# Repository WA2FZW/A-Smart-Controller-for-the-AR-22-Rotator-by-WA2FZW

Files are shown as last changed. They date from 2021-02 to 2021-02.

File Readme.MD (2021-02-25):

A Smart Controller for the AR-22 Rotator by WA2FZW
Version 5.4

The AR-22 rotator controller is an Arduino Uno based controller for the old
CDE AR-22 antenna rotator which replaces the clunk-clunk controller that the
original used.

The main features include the ability to turn the antenna in 1, 5 or 10
degree increments and the ability to control it with many of the rotator
control programs available such as the N1MM Rotor program.

The files provided here include the latest version of the software, a manual
describing how to build and use the controller and the Gerber files needed
to fabricate the 2 custom PCBs used.

Version 5.3

No changes to the software (Version 5.2 is the latest software version), but
Neal (WA9WYI) discovered a mistake on the power supply PCB; the pins on the
LM7812 regulator were reversed. The Gerber files for the power supply PCB
are corrected and identified as Version 5.3.

Document Update 9/4/2020:

Added information about the commands available on the serial interface. Not
sure why I never listed them in the original!

Update Jan 04, 2021 - Fixed a couple of typos in the docmentation and added
a "Table of Contents".

Version 5.4 - 2/24/2021

I made a number of changes to both the hardware and software and finally
fixed a problem that has been bugging me since the intial version!

Hardware Changes

In the hardware, I added more filtering on the power supply board and on
the controller board I added snubbing diodes across the relay coils (I
thought they were built into the relays; NOT) and added a bypass capacitor
in an effort to reduce the noise on the rotator pulse line.

One additional change on the controller PCB was to add a header connected
to the TX2/RX2 serial interface on the Arduino Mega. This is not used yet,
but I plan to add elevation control using a separate processor.

Software Changes

In the software, I made some changes to the timeout logic to deal with two
problems.

One problem this solves is the fact that there is some inertial delay when
the rotator initially turns on; the bigger the antenna, the more inertia!
The second problem was that sometimes the rotator was stopping with the cam
switch in the closed position which caused an immediate pulse upon the next
startup and the inertia delay was causing an immediate timeout.

Now when the rotator starts (or reverses direction), the cam pulse timeout
value is set to 2 seconds by the symbol INITIAL_TIMEOUT in the header file.
Once the controller has seen 2 cam pulses, the timeout value reverts to the
value of ROTATOR_TIMEOUT.

I also made a few changes in the code to improve performance and I added the
hooks for an interface to an elevation controller for my satellite antenna.

Note that the Version 5.4 software will run on the older hardware (Version
5.2 and later).

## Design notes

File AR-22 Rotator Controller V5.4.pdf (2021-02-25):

- Page 1 -

## A Smart Controller for the AR-22 Rotator Version 05.4

## © John Price – WA2FZW

## Table of Contents

- Page 2 -

- Page 3 -

- Page 4 -

## License Information

This documentation and the associated software are published under General Public License version 3. Please feel free to distribute it, hack it, or do anything else you like to it. I would ask, however that is you make any cool improvements you let me know via any of the websites on which I have published this or by email at WA2FZW@ARRL.net.

## Introduction

I had just finished up two Arduino (https://www.arduino.cc/) based ham radio projects; a BitX-40 (http://www.hfsigs.com/) QRP transceiver and a magnetic loop antenna and controller when I received an email from Mike, WV2ZOW asking if it might be possible to design a computer based controller for the old CDE AR-22 (http://www.radiomanual.info/schemi/ACC_rotator/CDE_AR-22R_user.pdf) (clunk-clunk) rotator. Without even a second thought, I replied something to the effect of “Piece of cake”! After all, I had spent a number of years at the phone factory (AT&T) computerizing things that were never designed to be computerized, so this seemed to be a project right up my alley.

The overall objective was to be able to control the rotator either manually or with the N1MM+ contest logging and rotator control software. (https://n1mm.hamdocs.com/tiki-index.php)

I looked at a number of similar projects online and one in the ARRL’s Arduino for Ham Radio (https://www.arrl.org/shop/Arduino-for-Ham-Radio) book and although I got a few good ideas, didn’t find any that really looked like they would accomplish what I wanted to do. My main issue with most of them was the software. I looked at one controller that has some 14K lines of code. My software has about 1,600 lines and about half of those are comments and blank lines inserted for clarity.

Well, it turned out not to be quite as simple as I first thought (definitely an understatement), but overall, it wasn’t totally impossible.

Thanks to Mike (WV2ZOW unfortunately now a SK) for all his help with the electrical issues encountered along the way.

Here, I’ll describe the hardware and software used in the project. The reader can build this exactly as described or use this description as a model for a different approach. I’ll try to point out all the wrong assumptions and mistakes I made along the way.

- Page 5 -

## Revision History

Changes in Version 2.0

In version 1.0, the azimuth was completely controlled by pulses generated by the cam operated switch inside the rotator itself. Those pulses were sent approximately every 6° of rotation.

In Version 2.0, interrupts from a software timer were used to generate pseudo index pulses approximately every 1° of rotation, which allowed the azimuth to be set within 1° (plus or minus a slight error).

Changes in Version 2.1

Version 2.1 included three hardware changes and one software change.

The first change which included both hardware and software was done to fix the problem of the Arduino rebooting whenever the N1MM+ Rotor program or the Arduino IDE serial monitor was started. A toggle switch labeled “Run/Update” was added to the back panel. This switch, when closed, places a 10uF capacitor between the Arduino’s reset pin and ground. It gobbles up the very brief reset pulse sent by the serial connection whenever the N1MM+ Rotor program or the serial monitor is started.

The reset pulse is generated via a connection on the Arduino board between the DTR (Data Terminal Ready) line from the serial interface to the reset line.

That same short reset pulse is also sent from the Arduino IDE whenever we need to load new software into the Arduino, thus the switch must be opened to disconnect the capacitor whenever new software needs to be loaded.

Associated with this modification, the back panel “Reset” button was disconnected from the Arduino’s reset pin and moved to D19 (an interrupt enabled pin). Pressing the button will now do two things; first, it will save the currentAzimuth then perform a software initiated reboot.

The second minor hardware change was to add diode D2 (I renumbered them on the schematic also) between the output of the LM7812 regulator and the Arduino’s Vin pin. The connection for the Power indicator LED is now between the regulator and D2.

- Page 6 -

This was done because in Version 1.0, the LED would light when the controller was connected to a computer via the USB connection regardless of whether the internal power supply was turned on or not. This was because when the Arduino was connected to the computer via the USB port, there was approximately 4.5V on the Vin pin; that was totally unexpected. Now, the Power LED only lights when the internal power supply is on. When the USB connection is present, the LCD display will continue to light up regardless of the state of the internal supply.

Note that the Version 2.1 or Version 3.0 software will run on controllers that do not have these hardware modifications.

A third hardware modification was to build the power supply on a separate circuit board that mounts on top of the interconnect board. The circuitry was not changed (other than the addition of ‘D2’); this modification just made a little more total real estate available and made it simpler to wire it all up.

Changes in Version 2.2

In version 2.2, two new functions were added, and the timing parameters were tweaked.

The first new function is Backup(), which moves the rotator slightly off the end stop whenever it times out (either in normal use or calibration). The second is Ck_Reboot(), which checks to see if the operator pushed the reset button on the back panel. It contains the same logic that was originally coded in the Loop() function, but since it also needed to be checked in the Calibrate() function, it was converted into a stand-alone function.

In conjunction with the addition of the Backup() function a new definition was added called CAL_ADJUSTMENT, which defines the number of degrees to back off the end stop.

The timing tweaks included reducing the timer interrupts from 141mS to 140mS and changing the rotator timeout from 1 second to 850mS.

- Page 7 -

Changes in Version 3.0

After adding the timer interrupt in Version 2.0, I noticed that the rotator was not turning a full 360° when commanded to do so (either via the serial interface or the encoder). Hooking the rotator up to the original clunk-clunk box, I also discovered that the same thing was happening; even though the original controller recorded 60 clunks, the rotator did not turn a full 360°.

Making some careful measurements, I found that it was coming up about 9° short. Doing a little math, I calculated that the cam switch was actually producing pulses about every 5.85° instead of the advertised 6°.

This necessitated a complete overhaul of the azimuth computations.

Rather than incrementing or decrementing the currentAzimuth by a whole degree for every timer or cam pulse received, the azimuth is adjusted by 0.975 degrees (5.85/6) for each pulse. Rather than attempting to use floating point math, all the internal azimuths and adjustment factors are multiplied by 1000 internally and the long data type is used to store the numbers.

Also in Version 3.0, because of all the things that might need to be tweaked for a particular rotator, I moved the definition of the number of degrees per cam pulse and all the variables associated with the timer interrupt interval, cam pulse detection, LCD parameters and encoder pin definitions to the My_Rotator.h header file to make it easier for someone to find and tweak these parameters.

Changes in Version 4.0

Although I finished the initial version of this project some 6 months ago, I hadn’t actually used the controller in a real operating environment until I finally got a 6 meter beam on the roof just before the 2018 ARRL June VHF contest. In operating the contest, the first thing I discovered was that it took an awful lot of turns of the azimuth (encoder) knob to turn the antenna 180°. The second thing I noticed was that in the brief times when I was repositioning my fingers on the knob to turn it more, sometimes the azimuth would be saved before I had finished setting the final target azimuth.

- Page 8 -

So, in Version 4.0, I made 2 hardware/software changes. First, I added a 3 position SPDT (center off) toggle switch to the front panel. This switch along with some software changes allows the operator to select the number of degrees to increment (or decrement) the target azimuth when turning the encoder knob. The increment can now be set to 1°, 5°, or 10°. A symbol definition (AZ_SW_INSTALLED) was added to the My_Rotator.h file to indicate whether or not said switch is actually installed.

If the switch is not installed, the azimuth increment is determined by the value set in the My_Rotator.h file for DEFAULT_INCR; it is set to 5° in the distributed software but can be changed to any value you like.

A second hardware change I made was to add another LED to the front panel which will indicate that the currentAzimuth has been saved in the EEPROM.

A second software change was to modify the algorithm for saving the azimuth. As noted above, I noticed that it would sometimes get saved before I had finished setting a new target azimuth. Now the azimuth will be saved 10 seconds from the last time the rotator stopped turning. This can be adjusted by changing the value of the symbol EEPROM_TIMEOUT in the “My_Rotator.h” file.

Changes in Version 4.1

In Version 4.1, I made a slight change to the calibration logic. In previous versions, when a timeout occurred due to missing a cam pulse, the currentAzimuth would get set to either 0° or 360° based on which direction the rotator was turning. It the timeout did not occur due to it hitting the end stop, it would now be way out of calibration.

Doing a calibration after such a timeout would often cause the rotator to turn through almost a full rotation to re-calibrate itself.

In order to correct this, a new variable, lastGoodAzimuth is introduced. This gets set to the currentAzimuth only after successfully seeing a sync pulse (hard or soft). In the calibration function, this variable is used to determine which way to turn the rotator to do the calibration instead of the possibly erroneous currentAzimuth.

- Page 9 -

Changes in Version 5.0 & 5.1

There are no significant software changes in Version 5.0 other than to reassign some of the Arduino pin numbers used.

What did change is the hardware. Using my newly acquired knowledge of how to design printed circuit boards, I decided to replace the hand-wired boards used in the first two of these I built. That also allowed me to fix a hardware bug in the first one that was just too hard to fix because of the way I built the hand-wired board for that one.

Version 5.1 fixed some bugs on the PCB and in the software.

Changes in Version 5.2

When testing Version 5.1 with a 2nd rotator, a problem showed up in that the rotator was hitting the mechanical end stop with the cam switch in the closed position, which caused a never-ending pulse to be sent to the controller and thus, the expected timeout at the end stop would never occur.

I made a number of attempts to fix this in the software without any luck and finally decided to re-design the entire pulse detection circuit. This also required a couple more minor tweaks in the code.

Cleaning up the pulse detection hardware and software also allowed me to further tweak the timing parameters.

Changes in Version 5.3

Neal (WA9WYI) discovered an interesting problem on the Version 5.0 power supply PCB; the pins for the LM7812 regulator were reversed! This was due to a rather DUMB mistake by yours truly. The redesigned power supply PCB is Version 5.3 and the Gerber files on GitHub have been updated to correct the problem.

If you have one of the older PCBs, you can mount the regulator vertically, upside down on the top side of the board or mount it on the bottom. The heat sink is not really necessary.

The schematic did not change.

- Page 10 -

Changes in Version 5.4

Version 5.4 makes some changes to both the software and the hardware. The primary goal of this version was to fix a problem that has been there since the initial version; periodically, when using the controller with a PC program such as the N1MM Rotor program (https://n1mmwp.hamdocs.com/setup/interfacing/) or the SatPC32 satellite tracking program (http://www.dk1tb.de/manual_e.htm) the USB connection between the controller and the PC would drop. It seems to be fixed!

Hardware Changes

In the hardware, I added more filtering on the power supply board and on the controller board I added snubbing diodes across the relay coils (I thought they were built into the relays; NOT) and added a bypass capacitor in an effort to reduce the noise on the rotator pulse line.

One additional change on the controller PCB was to add a header connected to the TX2/RX2 serial interface on the Arduino Mega. This is not used yet, but I plan to add elevation control using a separate processor.

Software Changes

In the software, I made some changes to the timeout logic to deal with two problems.

One problem this solves is the fact that there is some inertial delay when the rotator initially turns on; the bigger the antenna, the more inertia!

The second problem was that sometimes the rotator was stopping with the cam switch in the closed position which caused an immediate pulse upon the next startup and the inertia delay was causing an immediate timeout.

Now when the rotator starts (or reverses direction), the cam pulse timeout value is set to 2 seconds by the symbol INITIAL_TIMEOUT in the header file. Once the controller has seen 2 cam pulses, the timeout value reverts to the value of ROTATOR_TIMEOUT.

I also made a few changes in the code to improve performance and I added the hooks for an interface to an elevation controller for my satellite antenna.

- Page 11 -

Note that the Version 5.4 software will run on the older hardware.

## Controlling the Rotator from a PC

The N1MM+ Rotator Control Program

The original intent of the smart controller was to allow it to work with the N1MM Rotor program. (https://n1mmwp.hamdocs.com/) That program supports a number of different types of rotators and communications protocols. Two of those protocols seem to be fairly standard. Those are Yaesu’s GS-232 protocol (http://www.radiomanual.info/schemi/YAESU_ACC/Yaesu_GS-23_GS-232_user.pdf) and HyGain’s DCU-1 protocol. (https://www.hamsupply.com/wp-content/uploads/2015/11/Rotor-EZ-Protocol.pdf)

I originally thought it might be a good idea to design the AR-22 controller so that I could support either protocol, which might allow it to be used with other contest logging programs, but in the end, decided that the GS-232 protocol was much easier to implement and it seemed to have more capabilities than the DCU-1 protocol, including support for 2-axis systems (not implemented in the AR-22 software).

The N1MM Rotor program doesn’t even use the full basic GS-232 protocol. The only commands implemented seem to be:

Mnnn | Turn the rotator to the azimuth specified by nnn.
C | Ask the rotator what its current azimuth is.
S | Stop the current command.

The N1MM Rotor Control program can be used as a stand-alone controller, or it can be used in conjunction with the N1MM+ Contest Logging program, which determines an approximate antenna azimuth based on the coordinates of the station using the software and the station being communicated with’s call sign.

Since the AR-22 software emulates the Yaesu protocol, when setting the N1MM Rotor program up, you have to tell it that the AR-22 is a Yaesu type rotator. You can also give it a unique name.

The N1MM Rotor program communicates with the AR-22 controller using a USB-2.0 port running at 9600 baud (which can’t be changed in the N1MM Rotor program). The N1MM+ Logging software also supports the ability to network a number of computers together for multi-operator contest operations.

- Page 12 -

Satellite Tracking with SatPC32

More recently, I’ve started to play with the amateur satellites and have been using the SatPC32 (http://www.dk1tb.de/indexeng.htm) program to track them and control my Icom IC-9700. SatPC32 is the current gold standard satellite tracking program. It has a rotator interface named ServerSDX which works with the controller. The setup is a bit confusing, but how to set the rotator up is very clearly explained in the help files for the program.

ServerSDX also supports elevation control and in Version 5.4 of the software and hardware I’ve added some hooks to add elevation control capability to the unit. For a bit more information about this see the Coming Attractions section of this document.

Controlling the Rotator via the Serial Interface

Although the rotator controller can be used with the N1MM Rotor program as described above, it can actually be controlled by any terminal emulator program (or the Arduino IDE’s Serial Monitor) capable of communicating with the processor via the USB port.

The USB port is set to operate at 9600 baud in the software as that is the baud rate hard coded in the N1MM Rotor program (you can change it if you like).

There are actually a number of other commands that can be sent to the controller in addition to those listed above; here is the complete list:

'A' or ‘S’ Stop command; cancels the last command and rotation
'C' | Ask for current azimuth; responds with “AZ=nnn”.
'L' | Rotate CCW to endstop
'R' | Rotate CW to endstop
'Maaa' | Rotate to specific azimuth
'F' | Start full calibration
'Zaaa' | Initialize azimuths
‘Waaa ee’ Turn to a specific azimuth and elevation

The ‘Z’ (zap) command is not part of the Yaesu protocol. I added it to facilitate testing and debugging. It sets both the currentAzimuth and targetAzimuth variables to the specified value (limited to the valid range of 0 to 360 of course) and saves the setting in the EEPROM.

- Page 13 -

Other Rotator Control Possibilities

Since the AR-22 controller software implements all of the basic Yaesu rotator commands, it will probably work with any PC based rotator control software which supports the GS-232 protocol.

Please note that the complete GS-232 command set is not implemented as some of the commands are just cannot be applied to the AR-22 rotator.

For anyone proficient at writing code for the PC or maybe a Raspberry Pi, you could also write your own program. If anyone does so, please let me know!

## The Controller Hardware

There are only a few major components in the controller hardware; specifically:

- The Arduino Mega2560 R3 (https://store.arduino.cc/usa/arduino-mega-2560-rev3) processor.
- An I2C 1602 2 line by 16 character LCD display. (https://www.amazon.com/SunFounder-Serial-Module-Display-Arduino/dp/B019K5X53O?hvadid=312760964359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)
- A Keyes KY-040 Rotary Encoder (http://henrysbench.capnfatz.com/henrys-bench/arduino-sensors-and-input/keyes-ky-040-arduino-rotary-encoder-user-manual/)
- A power supply to provide AC for the rotator motor and DC to power the Arduino and its peripherals.
- A custom shield containing the motor control relays and a circuit to convert the MOTOR_INDEX pulse from AC to DC plus the interconnections between the peripherals and the Arduino’s I/O pins.
- A custom shield containing the power supply circuitry.

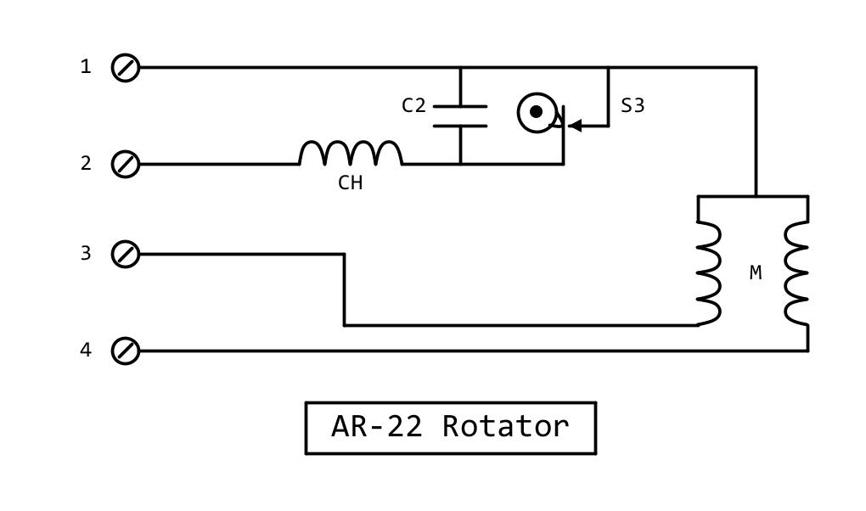
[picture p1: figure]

- Page 14 -

The Rotator Itself

Here is the schematic for the electrical components of the AR-22 rotator itself:

‘C2’ is 0.22uF @ 400V, and ‘CH’ is 15 turns of wire 3/8” in diameter.

In the original controller box, terminal ‘1’ is connected to one side of a (not center) tapped transformer, and terminal ‘2’ is connected to the other side of the transformer through the clunk-clunk solenoid.

Grounding terminal ‘3’ or ‘4’ starts the motor rotating in one direction or the other.

‘S3’ is operated by a cam and sends a pulse to the control box approximately every 6° of rotation.

The transformer used in the original controller is a custom transformer that CDE must have designed specifically for the controller (their main business was always capacitors and transformers). The original transformer provided about 36V on one side of the tap (connected to terminal ‘1’ on the rotator) when the motor wasn’t running, and 6.3V on the other side of the tap (for the #47 light bulb). The motor voltage is about 28V when the motor is operating.

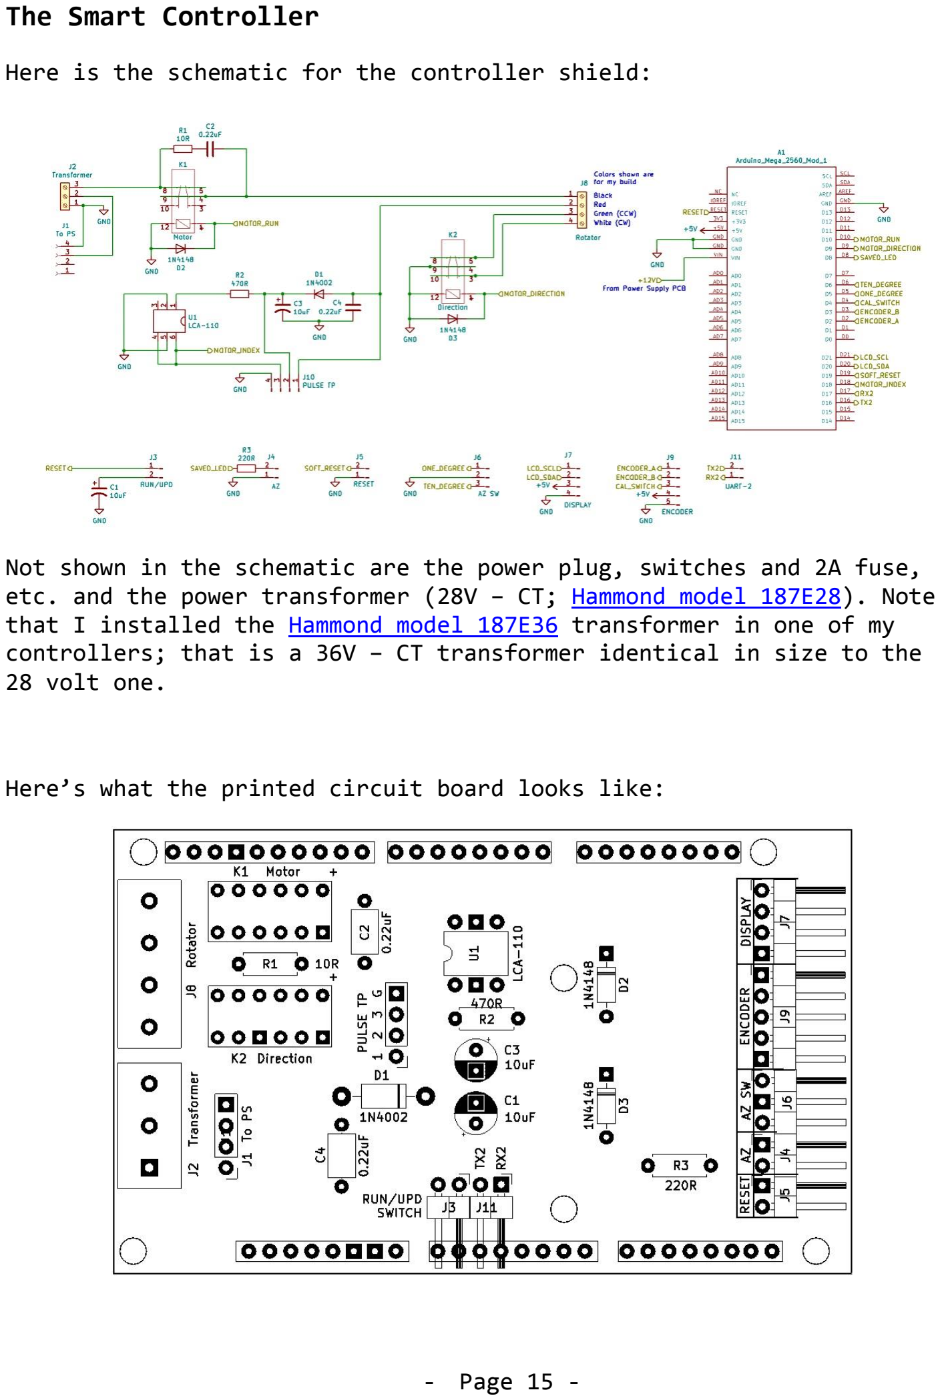
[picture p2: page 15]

- Page 15 -

The Smart Controller

Here is the schematic for the controller shield:

Not shown in the schematic are the power plug, switches and 2A fuse, etc. and the power transformer (28V – CT; Hammond model 187E28). (https://www.mouser.com/ProductDetail/Hammond-Manufacturing/187E28?qs=PRAnc%252blXlHhlx%2FRo63C%252bsw%3D%3D) Note that I installed the Hammond model 187E36 (https://www.mouser.com/ProductDetail/Hammond-Manufacturing/187E36/) transformer in one of my controllers; that is a 36V – CT transformer identical in size to the 28 volt one.

Here’s what the printed circuit board looks like:

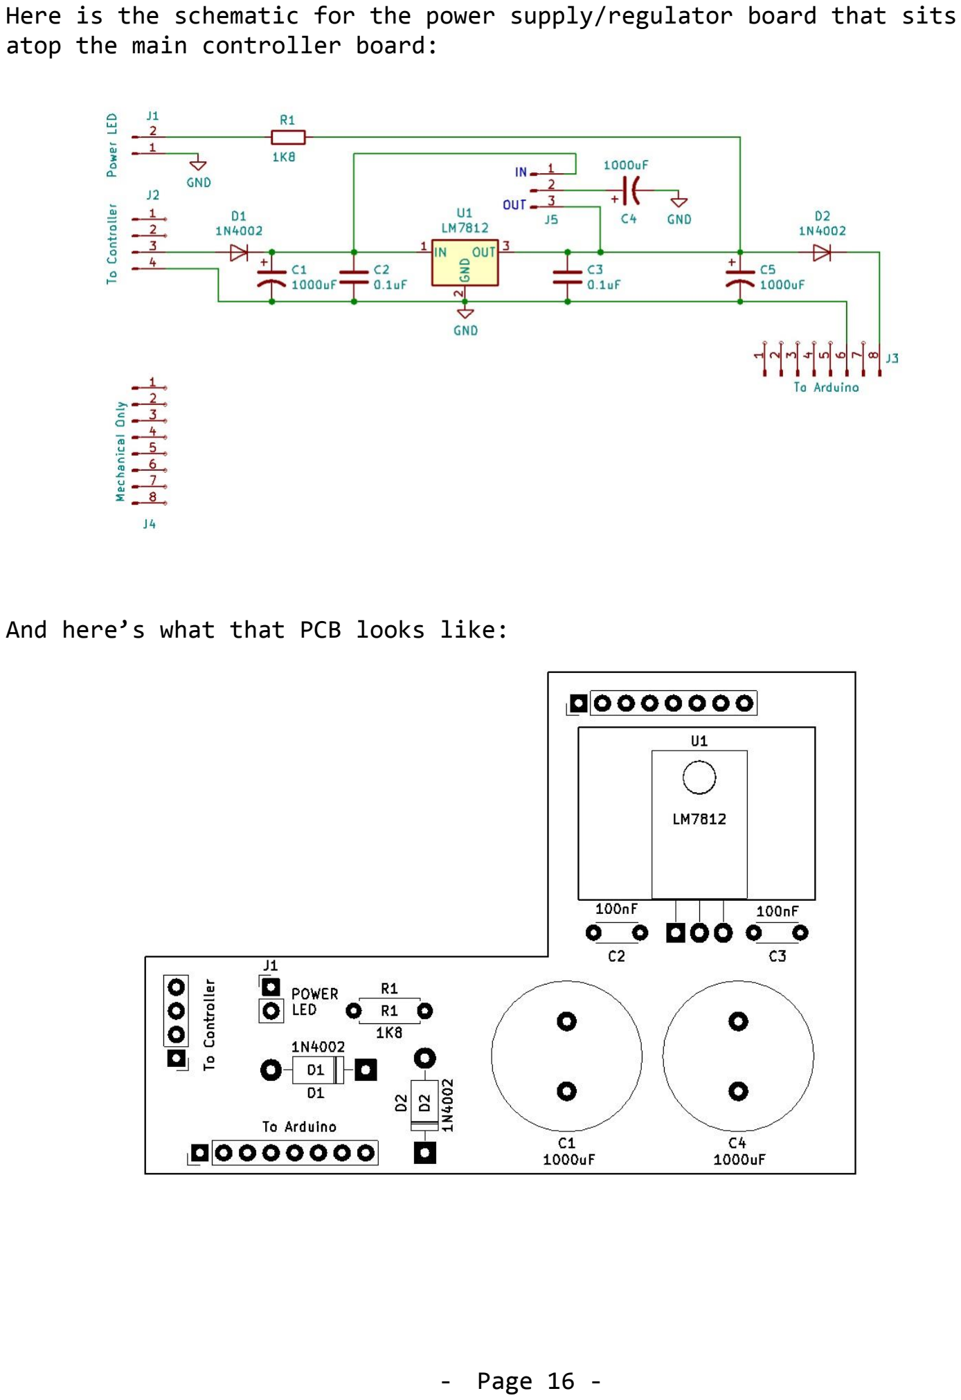
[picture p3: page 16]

- Page 16 -

Here is the schematic for the power supply/regulator board that sits atop the main controller board:

And here’s what that PCB looks like:

- Page 17 -

In the original clunk-clunk box, power was only applied to the power transformer when the dial was turned to start the rotator moving. Here, I not only use the transformer to power the rotator motor, but also as part of the DC power supply for the Arduino and its associated components, so it will always be turned on.

The original controller included a thermal protection switch on the primary of the power transformer; the smart controller omits it. In years of using the AR-22, I never had it activate. I believe it primarily came into play in the case where the rotator hit the mechanical end stop and the operator did not manually move the solenoid lever on the bottom of the box to calibrate the controller within a reasonable amount of time.

I determined that the thermal switch was unnecessary in the smart controller as the transformer used seems more robust than the original transformer and the software shuts down the motor automatically whenever the end stop is hit.

The top half of the transformer secondary provides 28 volts to the motor through ‘K1’, and grounding the other end of one or the other of the motor coils via ‘K2’ determines the direction of rotation. In the original clunk-clunk box, that was done by one of the cleverest mechanical switches I’ve ever seen that was part of the dial mechanism.

Here, the software will set the direction of rotation by activating (or not activating) ‘K2’. After a slight delay, ‘K1’ will be then be activated to start the rotation.

The relays I used (https://www.jameco.com/webapp/wcs/stores/servlet/ProductDisplay?catalogId=10001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) for ‘K1’ and ‘K2’ have 5V coils and contacts rated for 2A. The rotator motor draws just a bit over 2A, so since the relays are actually DPDT relays, I’m using both sets of contacts just to be on the conservative side. The relay coils draw 30mA, so they can be operated directly from the Arduino I/O pins, which are rated for a maximum of 40mA.

Note the combination of a 10Ω resistor and 0.22uF capacitor across the ‘K1’ contacts. This RC circuit prevents arcing of the ‘K1’ relay contacts when the motor is turned off. There is no such protection on the direction relay (‘K2’) as that one is never operated by the software while power is being supplied to the rotator through ‘K1’.

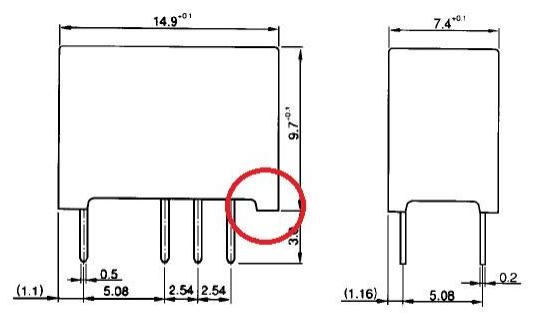
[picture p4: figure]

- Page 18 -

Something to note about these relays; they have little bumps on the bottom side corners as shown here:

If you’re going to solder them into the board, it’s not a problem, but they don’t socket well. I used a pair of flat cutters to cut the bumps off, but be careful on the end where the pins are close to the corner.

Terminal ‘2’ on the rotator is used to send pulses back to the controller via a cam operated switch that is closed momentarily every time the rotator moves about 6°. In Version 5.2, the entire pulse detection circuit was modified to use a solid state relay in place of the reed relay formerly used.

‘C3’ is the motor starting capacitor (https://www.amazon.com/gp/product/B00EQI3HZ2/ref=od_aui_detailpages00?ie=UTF8&psc=1) (not shown on the schematic; it is connected between terminals 3 and 4 of the rotator connection) and has a value of approximately 140uF and an operating voltage of 165VAC.

Summary of Arduino input/output pin usage

These are the pin assignments for the Arduino Mega 2560:

- D0 | USB Interface Receive
- D1 | USB Interface Transmit
- D2 | ENCODER_PIN_B
- D3 | ENCODER_PIN_A
- D4 | CAL_SWITCH (encoder pushbutton)
- D5 | ONE_DEGREE (1 degree switch)
- D6 | TEN_DEGREE (10 degree switch)

- Page 19 -
- D8 | SAVED_LED (Azimuth saved LED)
- D9 | MOTOR_DIRECTION (Relay ‘K2’)
- D10 | MOTOR_RUN (Relay ‘K1’)
- D11 | Reserved for Timer1 PWM output signals
- D12 | Reserved for Timer1 PWM output signals
- D13 | Reserved for Timer1 PWM output signals
- D16 | UART #2 Transmit (for the elevation controller interface)
- D17 | UART #2 Receive (for the elevation controller interface)
- D18 | MOTOR_INDEX (Interrupt enabled pin )
- D19 | SOFT_RESET_PIN (Interrupt enabled pin)
- D20 | LCD_SDA (I2C Data Line)
- D21 | LCD_SCL (I2C Clock Line)

Note that some encoders found online are wired backwards. If you have that issue, simply flip-flop the pin definitions for pins ‘A’ and ‘B’.

## Construction

The Controller Board

The relays and headers to connect the Arduino to the LCD, rotary encoder and a few other things are all mounted on the main controller board.

Besides changing the reed relay to an SSR in Version 5.2, I also added the “PULSE TP” header to the board to make it convenient to use an oscilloscope to look at the raw pulse from the rotator, the rectified and filtered pulse and the signal going to pin D18 of the Arduino.

The pins are numbered 1 to 3 on the PCB:

1. The pulse line directly from the rotator
2. The rectified and filtered (10uF) pulse from the rotator
3. The output of the LCA-110 SSR

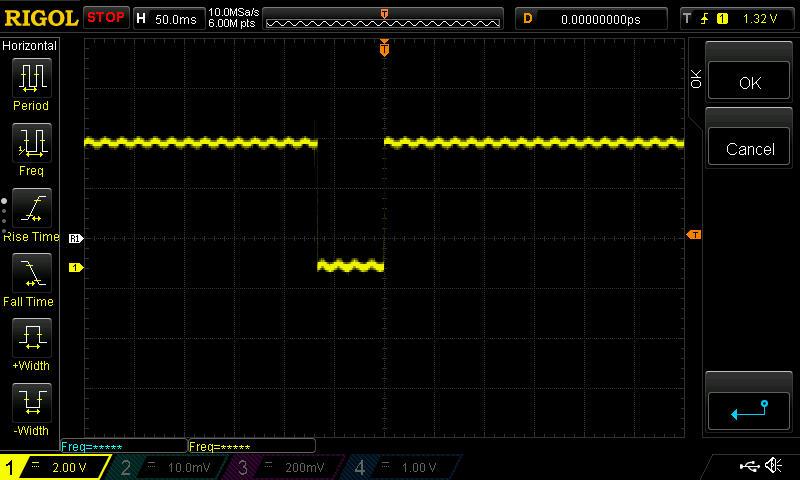
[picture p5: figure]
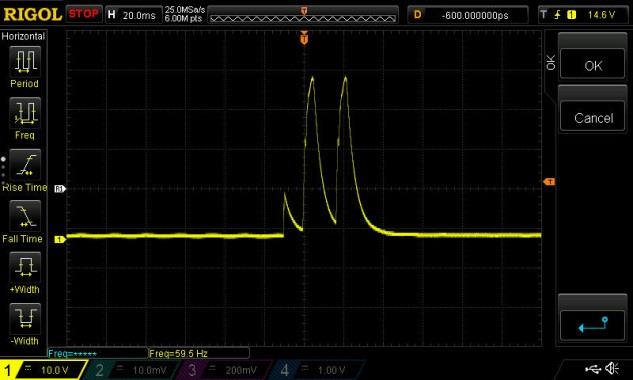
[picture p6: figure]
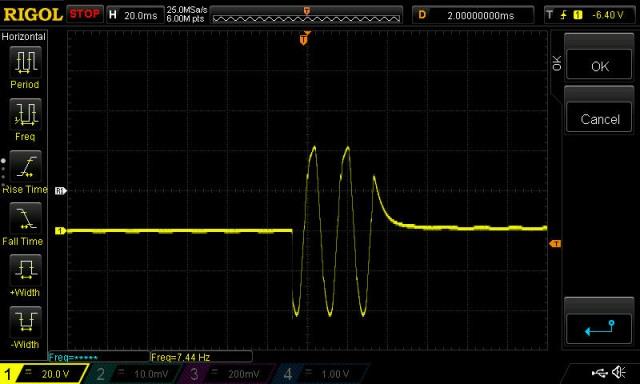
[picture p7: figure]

- Page 20 -

Here are some scope traces taken at the test points; this is the output of the LCA-110 SSR, which is what the processor sees (Test Point #3):

And here are the scope traces for the raw pulse from the rotator (Test Point #1) and the rectified and filtered pulse (Test Point #2):

Note that the controller these were taken on has the 36V transformer. The actual voltages would be slightly less with the 28V transformer.

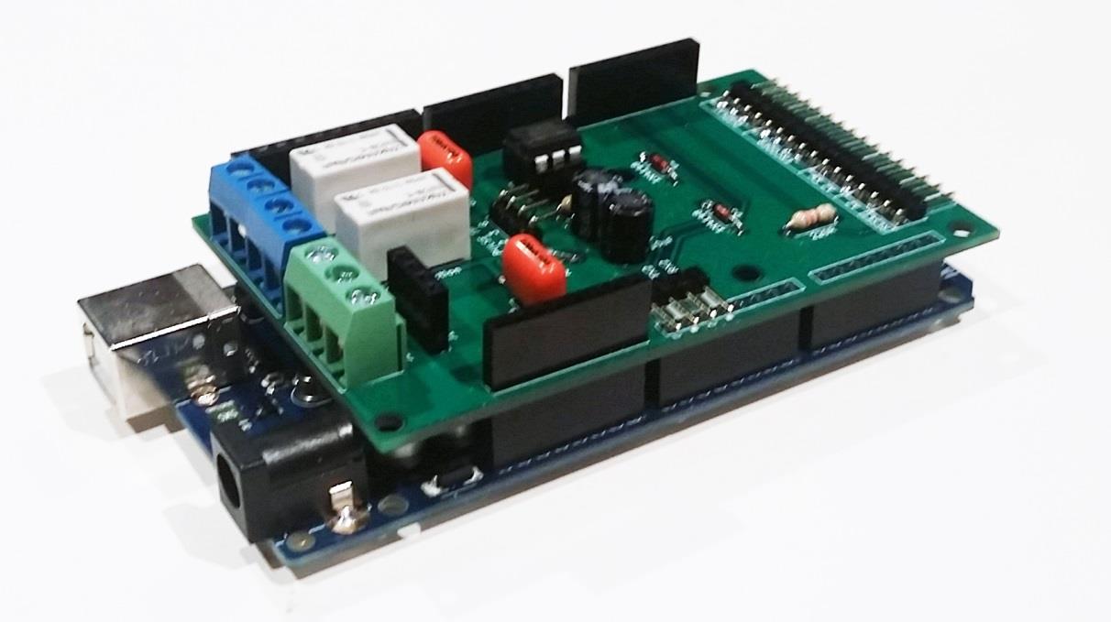
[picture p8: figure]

- Page 21 -

Here’s what the controller board looks like mounted atop the Arduino Mega:

The right angle male headers on the right side of the picture are the connections for the LCD, encoder, reset button and the Run/Update switch.

The right angle connector on the side of the board toward the camera is the connection to the “Run/Update” switch on the rear panel and the provision for the TX2/RX2 serial interface. There wasn’t room to put these with the rest of the connectors.

A word about the purpose of the Run/Update switch; the Arduino IDE sends a brief DTR pulse when it wants to update the software. This pulse also gets routed to the “Reset” pin of the Arduino. If the Arduino doesn’t see new software in a couple of seconds, it simply reboots. Unfortunately, N1MM Rotor program sends the same pulse when it starts, which causes the processor to reboot. The switch puts a 10uF capacitor across the “Reset” pin when it is in the “Run” position. The capacitor gobbles up the DTR pulse thus preventing a reboot. To load new software, the switch must be changed to the “Update” position.

The screw terminal headers on the left are for the rotator and the transformer, where we want to use a heavier gauge wire for the connections.

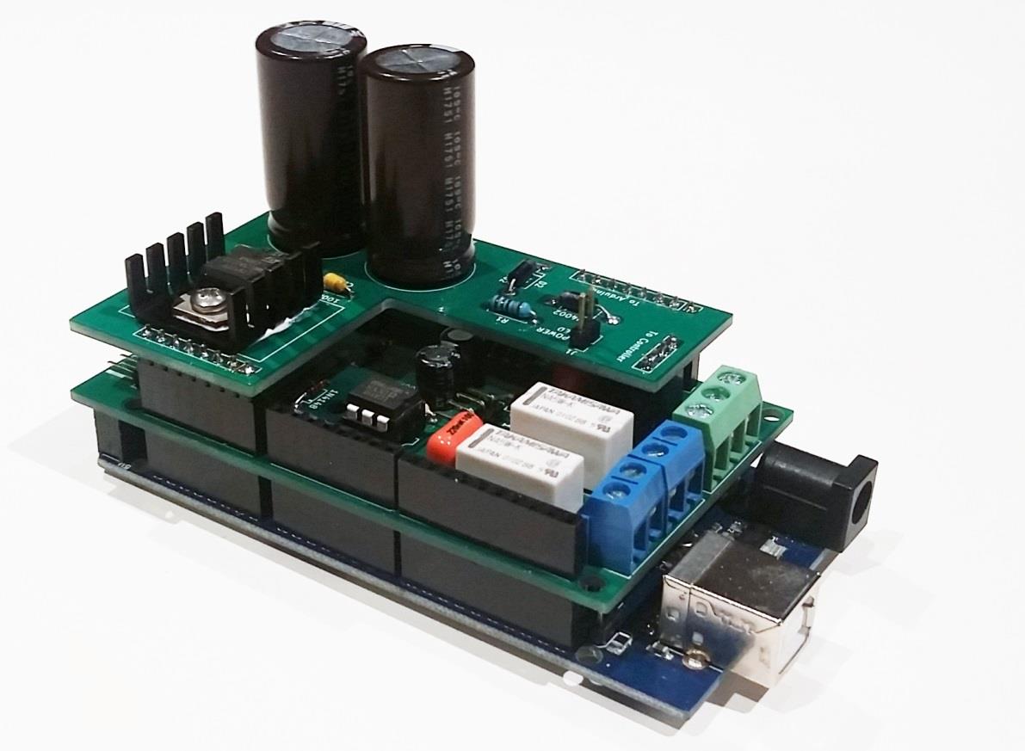
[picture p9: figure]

- Page 22 -

The four-pin female header just behind the screw-terminal headers provides a connection between the ground and center tap leads from power transformer to the power supply board.

Power Supply Board

To provide a bit more real estate on the interconnect board, in Version 2.1, the power supply components and connection to the power LED were moved to a separate circuit board that mounts atop the interconnect board. This also allowed more room for a better heat sink for the regulator which is not really required.

Here’s what the Version 5.4 power supply board looks like mounted on top of the stack. The vertical pin header is the connection for the power LED.

Metal Work

The enclosure I used is from Circuit Specialists. (https://www.circuitspecialists.com/metal-instrument-enclosure-la-6.html) They have a good assortment of enclosures for reasonable prices. I’ve used this same enclosure on two other projects already.

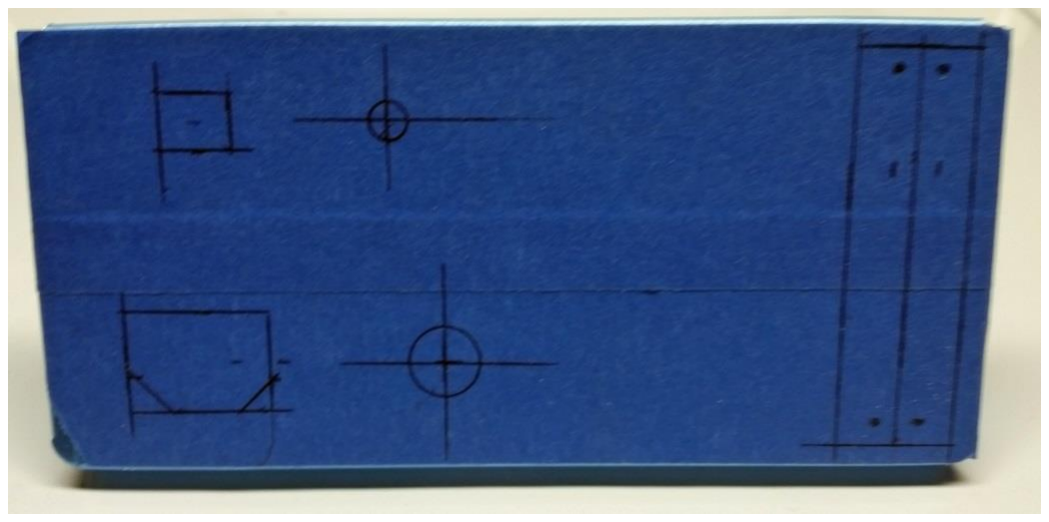
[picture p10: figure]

- Page 23 -

I’ve seen a lot of nice projects where the builders have had issues with doing a good job of cutting holes; particularly ones that aren’t round.

A couple of tools that I find to be an absolute necessity are a metal nibbler; mine is an Adel Nibbler (http://www.adelnibbler.com/) (it’s a bit pricey, but worth it), and a step drill (https://www.homedepot.com/p/Milwaukee-3-16-in-7-8-in-x-1-16-in-4-Step-Drill-Bit-48-89-9204/204312639) (I have 2 different sizes). Again, not the cheapest tool, but it makes much nicer holes (particularly big ones) than regular drill bits. Regular drill bits make holes that are slightly triangular according to my high school metal shop teacher.

The first step in doing nice metal work is to make a good drawing of what you want to do, as shown below in the section titled “Labeling”. Then, you need to transfer that drawing to the metal. I cover the metal with masking tape and then using my “blueprint” re-draw the plan on the masking tape. Note the masking tape also keeps you from scratching the metal (unless you really slip up). Use a square to make sure all the lines are parallel to the edges of the panel or box.

Here’s the (Version 1.0; no “Run/Update” switch or “Reset” button) back panel ready to be cut and drilled:

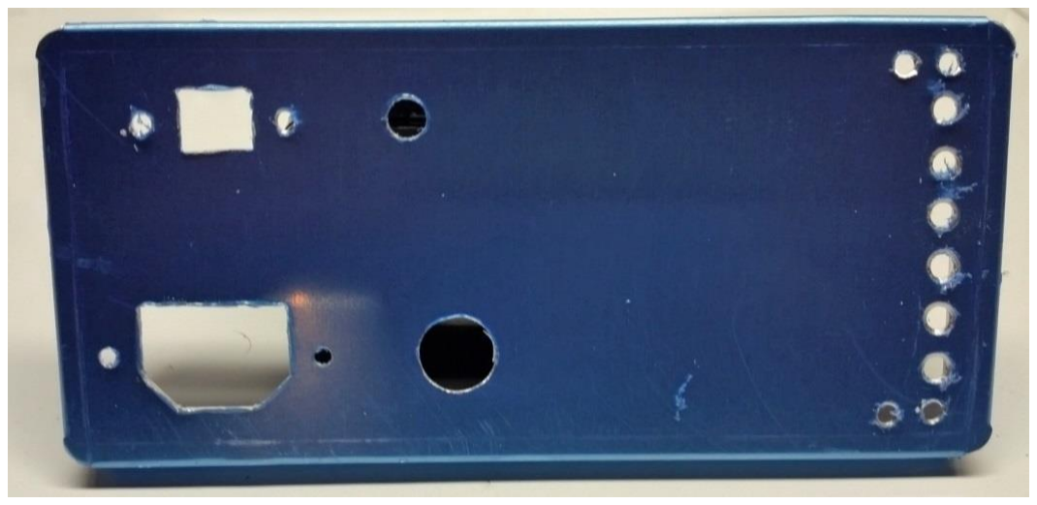
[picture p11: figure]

- Page 24 -

And here’s what it looks like after drilling and cutting (it’s not really blue; that’s a protective plastic coating that comes on the panel):

Labeling

A few of my friends that have been following and kibitzing on the project asked how I managed to do such a neat job of labeling the front and rear panels. The labeling was done using DIY decals. These come in two types. The ones used here (https://www.amazon.com/gp/product/B077TMFVL9/ref=ppx_yo_dt_b_asin_title_o01__o00_s00?ie=UTF8&psc=1) have a clear substrate. You can also get them with a white substrate if you want white lettering on a colored background.

I used one large decal each for the front and rear panels, which is why you don’t see the outlines of individual labels.

I made them using Microsoft Word. I scanned full size drawings of the front and rear panels and inserted them into a Word document. Make sure Word doesn’t automatically scale the pictures, which it will if the margins on the document are set too small. Print the document and make sure it lines up with your original drawing before proceeding any further.

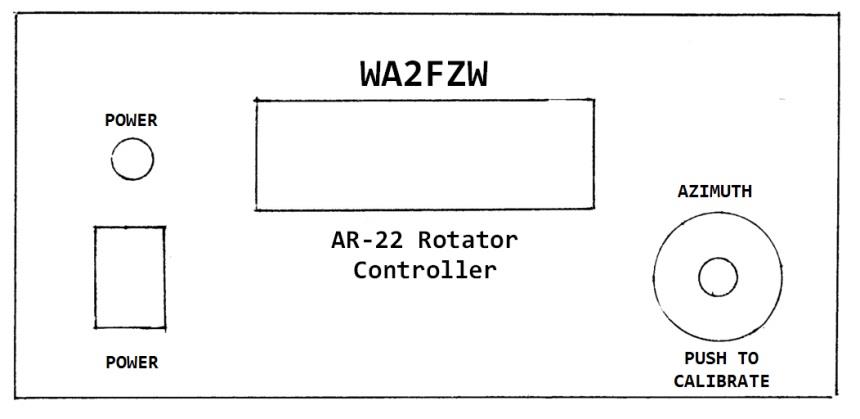
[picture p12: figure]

- Page 25 -

Once that is done, you can use Word to create textboxes to contain the label text, and you can drag them around to position them however you please. You can also use any font and color of your choosing. Here is my front panel drawing with the labels added in Word:

Once you have all the text where you want it, delete the drawing, which will leave you with a document containing just the labels (save it under a separate name), which you can now print on the decal paper. From there, follow the instructions for the particular transfer paper you are using.

I always print the decals on plain paper (or drafting vellum) first then lay that over the panel just to make sure everything is where I want it.

When you print the decal sheet, it is also important to set the printer options for “Glossy Photo Paper” and “Fine” or “High Quality” printing. I tried using “Best Quality” printing, but found that my printer puts way too much ink on the decal in that mode which makes it too easy to smear. Whichever you use let the ink dry for a couple of hours before doing anything else.

The decal instructions tell you to spray the decal with a number of coats of clear acrylic spray; I use Krylon crystal clear although I guess you could also use a satin finish.

Before applying the decals, be sure to remove any burrs around the holes. Any irregularities in the surface will make it hard to apply the decal smoothly, as it will cause bubbles under the decal.

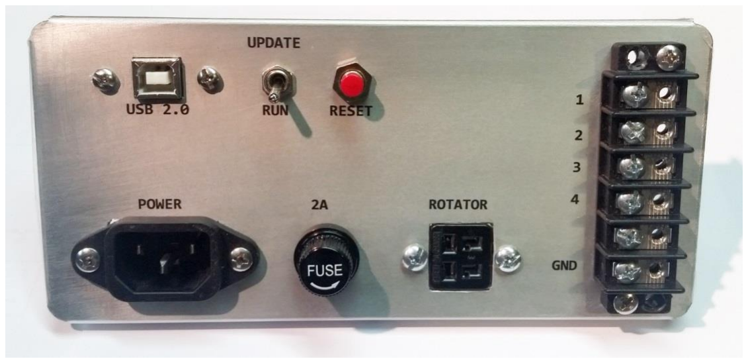
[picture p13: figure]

- Page 26 -

It is also important to make sure the surface is perfectly clean. I initially use prep-sol (available at the local auto parts store), sometimes followed by MEK. Do NOT use mineral spirits or turpentine, as they leave an oily residue. The prep-sol does not leave any film. Make sure your hands are really clean, or better yet, use doctor gloves (non-powdered). If you want to use the MEK on a painted surface, test it first to make sure that it’s not going to remove the paint.

Once you have the decal lined up on the panel, use a sharp razor blade or X-Acto knife cut “Xs” in the big holes (like the one for the display). This seems to make it easier to smooth the bubbles out of the decal.

After the decal has had a few hours to dry thoroughly, trim any excess around the edges and the holes with a razor blade or X-Acto knife. You can also use a fine file or emery board. I always give things a final coat of clear Krylon which I figure helps seal the edges of the decal.

And here’s the completed rear panel:

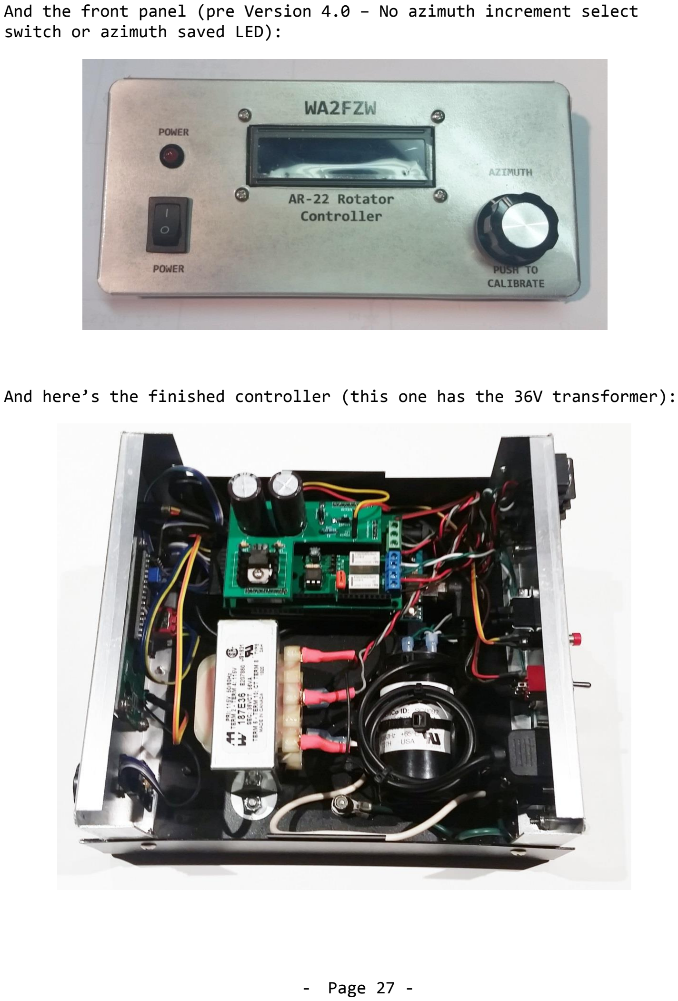
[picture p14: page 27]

- Page 27 -

And the front panel (pre Version 4.0 – No azimuth increment select switch or azimuth saved LED):

And here’s the finished controller (this one has the 36V transformer):

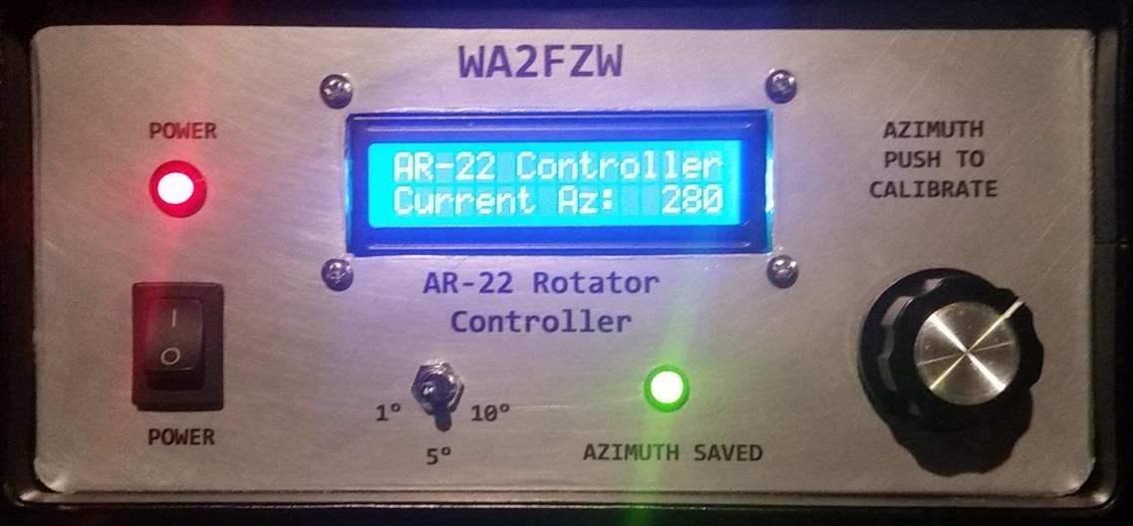
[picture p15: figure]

- Page 28 -

This picture shows the additional switch and LED added in Version 4.0.

## The AR-22 Controller Software

I chose the Arduino Mega2560 R3 (https://store.arduino.cc/usa/arduino-mega-2560-rev3) (I actually used a non-Arduino clone) as the processor, because of the increased interrupt handling capability of that version over other versions of the Arduino.

The Arduino is programmed primarily using the “C” language, although the Arduino Interactive Development Environment (IDE) (https://www.arduino.cc/en/Main/Software) also supports “C++”. In the Arduino world, “C++” is primarily used in the development of standard libraries as opposed to user programs.

Note that the liquid crystal display and the rotary encoder are handled as objects.

The Arduino has a built in bootstrap program that runs whenever it is powered up, reset or when new software is loaded into it. I assume this bootstrap program takes care of basic initialization functions for the Arduino hardware itself, and then it calls two user developed functions; setup() and loop().

- Page 29 -

The setup() function does just what it says. The developer puts things in here that must be initialized in order for the main part of the program, i.e., the loop() function to perform whatever task the software is intended to do. I’m not going to address all the things that one can do with the Arduino, nor am I going to describe how to write a “C” program. There are many fine books and online resources available for that. I highly recommend “Beginning C for Arduino, Second Edition: Learn C Programming for the Arduino”, by Jack Purdum (https://www.amazon.com/Beginning-Arduino-Second-Learn-Programming/dp/1484209419) as a great tutorial for both the beginner and experienced programmer.

What I will describe here, are the main functions of the AR-22 controller program and give a high level description of how each of the functions works.

General Logic

Before starting to describe the software in any level of detail, there are a few things the reader should understand.

First of all, the AR-22 rotator itself has a cam operated switch that sends a pulse to the controller (our smart one or the old clunk-clunk box) that indicates it has moved about 6° in either direction. In Version 1.0 of the software, the azimuth resolution was controlled solely by pulses from the cam switch. In Version 2.0, a timer interrupt mechanism was added to provide pseudo index pulses approximately every 1° of rotation, thus allowing the rotator to be aimed more precisely. While that might be of little importance if the antenna being turned is a tribander or some other fairly broad-pattern antenna, it does become important if the rotator is being used to swing a many-element VHF or UHF array.

Note, as mentioned above, the amount of contact bounce in the cam switch is horrible, and in the early versions of the controller software, there was some rather convoluted software to deal with the problem. The hardware and software modifications in Version 5.2 pretty much eliminated the contact bounce problem and some additional modifications were made to the software.

- Page 30 -

The AR-22 can get out of calibration quite easily. The most common way this happens is when a movement of the rotator is followed by one in the opposite direction. When the index pulse that indicates the targetAzimuth has been reached is received, the rotation stops, but not immediately. Unlike some of the heavy duty rotators, the AR-22 has no brake, so even though the motor is turned off, rotation will continue because of the rotational inertia of whatever it is turning (the bigger the antenna, the more inertia).

If it stopped after receiving a real index pulse from the cam switch (as opposed to a pseudo pulse from the timer) it will have turned about 0.6° past the switch closure due to the debounce masking algorithm used. Upon starting in the opposite direction, it will receive another real pulse almost immediately.

The good news is that because of the 1° resolution in Version 2.0 of the software, the rotator will now be only 1° out of calibration as opposed to 6° as was the case in Version 1.0 of the software, and then, only if it stopped because of a hard pulse as opposed to a timer generated one.

After running the test rotator back and forth through various random azimuths for 5 minutes or more and then doing a calibration resulted in it only being a couple of degrees off.

Note that this software will probably also work with the old Alliance clunk-clunk rotators if the values of the timing parameters are adjusted for that rotator (more about this later).

The hardware would, however, have to be modified. The Alliance motor runs on 18 volts, so ‘T1’ would have to be changed. Since the center tap feeding the rectifier would then be providing only about 9 volts, the power supply circuity might also need to change.

Arduino Libraries

The software requires four libraries that are not part of the standard Arduino IDE.

One is for the rotary encoder. (https://github.com/brianlow/Rotary) The second is for the I2C LCD display, (https://github.com/fdebrabander/Arduino-LiquidCrystal-I2C-library) the third is for the timer, (https://github.com/PaulStoffregen/TimerOne) and the fourth for the software reset capability. (https://github.com/WickedDevice/SoftReset) All four are available on GitHub. (https://github.com/) Note that there are a number of libraries available for I2C type displays. The one referenced here works with the particular LCD I used. If you use a different one, you might need a different library.

- Page 31 -

Initial Definitions

Definitions in My_Rotator.h

In Version 3.0, I moved all the variables that might need to be tweaked for a particular rotator or the use of different components in the controller into the My_Rotator.h header file along with detailed explanations of why and how they might need to be modified.

The variables defined in My_Rotator.h are:

- BAUD_RATE; Sets the baud rate for the serial (USB) interface. The N1MM Rotor program can only run at 9600 baud. The SatPC32 program can run at up to 57,600 baud.
- ELEVATION if set to true, it indicates that the auxiliary elevation controller is attached and enabled. As this hasn’t been built yet, be sure to leave this set to false.
- PULSE_DEGREES; the number of degrees that the rotator turns for each pulse from the cam operated switch multiplied by 1000. Note that in the distributed software, this is set to 5.85 degrees, which is what I measured on the test rotator. Yours may require a slightly different value.
- AZ_ROUNDING; since the internal azimuths are no longer nice even multiples of 1°, we need to round them off before displaying them.
- timerInterval; in the distributed software is set to 137 mS. Again, this was based on the rotator I used for testing and how it is determined is described further on in this document.
- CAL_ADJUSTMENT; One of the things I discovered in testing is that there are actually more than 360° between the end stops on the rotator. CAL_ADJUSTMENT is the number of degrees to back up when the end stop is hit.
- PULSE_DEBOUNCE; the number of milliseconds needed to mask the contact bounce in the cam switch.
- ROTATOR_TIMEOUT; The number of milliseconds that are allowed to elapse without seeing a cam switch pulse indicating that the rotator hit the mechanical end stop.
- INITIAL_TIMEOUT; This is set to 2 seconds and is used as the cam pulse timeout when the rotator is first started. 2 seconds is the minimum amount of time I found to work reliably for my test rotator.

- Page 32 -
- The parameters associated with the LCD display. If a different display is used, the size parameters need to change, and the I2C bus address might need to be changed.
- LCD_ADDRESS; The I2C address of the display. The standard I2C address for the LCD is 0x27. One of my units has one whose address is 0x3F. There are programs available to scan for I2C devices and report their address available on line if you’re not sure. If the display lights up, but doesn’t contain any information it’s a good guess that the address is wrong.
- The pin assignments for the rotary encoder. Some have the ‘A’ and ‘B’ pins reversed. If yours works backwards, just reverse the pin assignments.
- AZ_SW_INSTALLED; If the 3 position toggle switch to set the target azimuth increment is installed, the symbol should be set to true. If the switch is not installed, set the value to false.
- DEFAULT_INCR; If the toggle switch is not installed, this defines the number of degrees to increment (or decrement) the target azimuth for each click of the encoder. It also defines the number of degrees to increment or decrement the azimuth if the toggle switch is installed and is in the center/off position. It is set to 5° in the software as distributed, and may be changed to whatever value you like.
- EEPROM_TIMEOUT; The number of milliseconds to wait after the rotator has stopped turning to update the EEPROM.

Definitions in the Main Program

Before we even get to the setup() function itself, you will note that there are a lot of #define statements and other variable definitions and value assignments. These create symbolic names for any number of things used throughout the program. Any variables defined outside the scope of any particular function are global variables, which can be accessed and even modified by any of the functions that comprise the program.

The definitions and value assignments here include:

- Timeout parameters for the rotator itself, the display of the default “Hello” message and the EEPROM update.
- Definitions of the standard messages that are displayed.
- The final things done prior to the setup() function are to create global objects for the rotary encoder and LCD display.

- Page 33 -

The setup() Function

The setup() function takes care of initializing all of the peripherals that make up the controller. Although we could define a lot of things outside the scope of an actual function, other than creating the encoder and LCD objects and assigning values to specific variables, prior to the setup() function, we couldn’t actually perform the actions necessary to put the hardware components into the desired states.

This is what we do in the setup() function:

- Initialize the serial communications port. Note that the communications port can also be used for debugging using the Serial Monitor capability in the Arduino IDE, (https://www.arduino.cc/en/Main/Software) but not at the same time that the N1MM+ program is running. Also, note that the N1MM+ Rotor program is only capable of operating at 9600 baud.

I haven’t tried it, but I’ve used the VSPE program from Eterlogic (http://www.eterlogic.com/Products.VSPE.html) to allow 2 programs to simultaneously communicate with a radio using USB protocol; that might also work here.

- Compute the values for timerDegrees and maxAzimuth based on the definition of PULSE_DEGREES defined in the My_Rotator.h header file.
- Initialize the currentAzimuth, targetAzimuth and the flags that indicate the state of the rotator. The value of currentAzimuth is read from the Arduino’s EEPROM, where it is periodically saved when the controller is in use.
- Configure the I/O pins used to control the rotator and make sure the two relays used to control the power and direction of rotation are both off.
- Initialize the liquid crystal display.
- Set up the encoder input pins.
- Define what to do when the encoder generates an interrupt.
- Define what to do when we get an index pulse interrupt.
- Set up the timer interrupt mechanism.
- Define the software reboot pin.

- Page 34 -

The loop() Function

Once the setup() function is finished, the loop() function runs forever. Using a number of sub-functions, it monitors all the inputs and produces required outputs with the exception of the rotary encoder, which is handled by an interrupt mechanism.

The loop() function proper does the following tasks:

- Sets the systemTime on each pass through the loop. We do this because the millis() function does not work correctly inside interrupt service routines.
- Calls the Say_Hello() function to announce that the program is running and looking for work to do.
- Calls the Get_Command function to see if there is any input from the USB interface and if so process the command.
- Sets the azMultiplier variables to the appropriate value as determined by the position of the front panel toggle switch or lack of it. This is used in the Read_Encoder() function to compute the target azimuth change each time the encoder is moved.
- Calls Display_Target(), which displays the targetAzimuth on the first line of the display if it was changed by the command processing functions or via movement of the rotary encoder.
- Calls Start_Rotator(), which will initiate any movement required by the most recent command.
- Calls Check_Timeout(), to see if too much time has expired since receiving the last MOTOR_INDEX pulse from the rotator.
- Calls Read_Pulse() to see if a MOTOR_INDEX or timer generated pulse was received, and if so, update the currentAzimuth and reset the timeout.
- Calls Check_Reversal() to see if the N1MM+ program or the operator via manual control requested a new azimuth requiring the rotator to reverse direction.
- If the rotator is not currently turning, it calls Update_Az() to see if the EPROM should be updated.
- If the rotator is not turning, it calls the Check_LCD() function to see if anything other than the hello message needs to be displayed.
- If the operator operates the encoder pushbutton, we call Calibrate() to recalibrate the rotator.

- Page 35 -
- Calls Ck_Reboot() to see if the operator pushed the reset button on the back panel.

Note that Check_Timeout(), Read_Pulse() and Check_Reversal() are only called if the rotator isRotating.

The Get_Command() Function

The Get_Command() function checks to see if any data has arrived at the Serial port, and if so, uses the Serial.peek() function to see what the first character is.

The Serial.peek() function doesn’t remove the character from the buffer, but rather just sees what it is. It also returns a zero value if there is no data in the buffer.

If there are one or more characters in the buffer, the function reads the entire command into the commandBuffer for later use in the Process_Command() function. Note the use of the Serial.readStringUntil function to read the command line. The N1MM Rotor program uses a return character as a command line terminator instead of the more common newline character. If you’re using a different controller program, that might need to be changed in the software.

Once the command has been read into the buffer, a switch statement is used to determine what the command is and take the appropriate actions. In versions of the software prior to Version 5.4 the command processing was done in a separate function.

The Start_Rotator() Function

Start_Rotator() first checks to see if the rotator is already in motion and if the currentAzimuth and targetAzimuth values are equal. If either is true, then the function just returns.

If the rotator needs to be turned, we figure out in which direction. If the targetAzimuth is greater than the currentAzimuth, the rotator needs to turn counter-clockwise. If the targetAzimuth is less than the currentAzimuth, the rotator needs to turn clockwise.

Based on that, the correct setting for the direction control relay is set and the value of deltaAzimuth is set to either + or –timerDegrees.

- Page 36 -

The rotator motor is then turned on, the isRotating flag is set to true, the pulseTime and debounceTime are recorded and the new target and current azimuths are displayed.

The Check_Timeout() Function

If the rotator is not currently turning, the Check_Timeout() function doesn’t do anything.

If the rotator isRotating, we check to see if the difference between the current systemTime and the pulseTime is greater that the rotatorTimeoutI limit. If it is, we assume it is because the rotator hit the mechanical end stop.

If a timeout occurs, the motor relays are turned off and the currentAzimuth is set to either maxAzimuth or minAzimuth depending on which way the rotator was turning. targetAzimuth is then set to the value of currentAzimuth. The isRotating flag is set to false and a timeout message is sent to the display.

The rotator takes a little over 45 seconds to complete a 360° rotation, and based on observations, a MOTOR_INDEX pulse is received on the average about every 806mS. To allow a little extra time, the ROTATOR_TIMEOUT is set to 850mS.

If a timeout occurs, we also flash the azimuth saved LED for about 1 second and save the now calibrated azimuth.

If a timeout occurs, the function returns a value of true. Otherwise it returns false. The return code is only used in the Calibrate() function.

In the process of testing Version 3.0, I discovered that there are actually more than 360° between the CW and CCW end stops in the rotator. To compensate, I added the Backup() function, which we use here to move the rotator away from the end stop approximately CAL_ADJUSTMENT degrees whenever it hits the stop

The Timer_ISR(), Pulse_ISR() and Read_Pulse() Functions

Logically, these three functions are part of the same processing logic associated with dealing with incoming MOTOR_INDEX pulses and timer generated pseudo pulses.

- Page 37 -

Timer_ISR()

Timer_ISR() is invoked by the Arduino’s interrupt handling mechanism by the TimerOne library logic every timerInterval mS (137mS for my rotator).

How is the 137mS number determined? This is important, because it might need to be a little different for different rotators. My rotator takes just a little over 49 seconds to complete a full 360° rotation. Based on timing tests for that particular rotator, index pulses from the cam switch are received on the average about every 806mS. That means it takes about 134mS for my rotator to turn 1°.

The value set for timerInterval needs to be slightly more than the time required for 1° of rotation (in my controller, it’s 4% more). This makes certain that the controller will see no more than 5 pseudo pulses from the timer before seeing the hard index pulse from the cam switch. If the value of timerInterval is too low, the controller might see 6 timer pulses between cam switch pulses, and thus, it will get totally out of calibration quickly.

Conversely, if the value of timerInterval is too high, the controller might only see 4 timer pulses between real index pulses, and again, will get out of calibration quickly. The closer the timerInterval value is to 1/6 of the hard pulse time, the more accurate the intermediate readings will be.

The function is pretty simple. If the rotator isn’t actually turning, it ignores the interrupt. If the value of pulseType is set to HARD_PULSE, it ignores the interrupt. Why this test, one might ask? Since the value of timerInterval is set to generate interrupts at slightly more than 1° intervals, we expect to get the 6th timer interrupt in a sequence slightly after seeing the real index pulse. This test indicates that a real pulse is waiting to be processed, and thus we should ignore the pseudo pulse.

If the above tests are both false, the value of pulseType is set to SOFT_PULSE and we’re done.

- Page 38 -

Pulse_ISR()

The cam switch in the rotator sends an AC pulse which is anywhere from about 40 mS to 100 mS in length depending on the mechanical adjustment of the switch in the rotator. In Version 5.2 and later, the AC pulse is rectified and filtered by a 10uF capacitor. The filtered pulse is then run through a solid state relay the output of which drives the interrupt enabled digital pin 18 of the Arduino.

In the setup() function we set up the interrupt to trigger on the trailing (rising) edge of the pulse. The logic here is to react to the initial state change and then ignore any other state transitions for a period of PULSE_DEBOUNCE mS (currently set to 15mS), although the new hardware configuration has almost completely eliminated any contact bounce problems as shown in the scope trace earlier in this document.

So what we do in the Pulse_ISR() function is quite simple. We check to see if the variable debounceTime is non-zero. If it is, that indicates that we have already seen the first state change in the series of pulses (bounces) and the function ignores the interrupt.

If debounceTime is zero, this is the first state change, so we set it to systemTime and also set pulseTime (used in the timeout logic) to systemTime. We use systemTime (updated on every pass thorough the loop() function) instead of a call to the millis() function as that function doesn’t work correctly inside interrupt service routines.

We also set the value of pulseType to HARD_PULSE and reset the interrupt timer to zero.

In Version 5.4 and later, this function also counts cam switch pulses and after 2 are seen sets the rotatorTimeout value to ROTATOR_TIMEOUT.

Read_Pulse()

The Read_Pulse() function, which is invoked from the main loop, first checks to see if the rotator isRotating. If not, it simply returns. As a double check, if the value of pulseType is NO_PULSE, it also returns.

- Page 39 -

If the value of pulseType is HARD_PULSE, we see if the PULSE_DEBOUNCE time limit has expired. If not, the function again, just returns. When this happens, we aren’t ignoring the pulse but rather deferring processing it until the PULSE_DEBOUNCE time expires. That works because we don’t zero out the debounceTime until the pulse has been processed, which is what keeps the Pulse_ISR() routine from resetting the pulse times.

Once the pulseTime expires or if the pulseType was SOFT_PULSE, we process the pulse, which is pretty simple; we increment or decrement the currentAzimuth based on the value of deltaAzimuth set in the Start_Rotator() function, zero out the debounceTime and set the pulseType to NO_PULSE.

Since we saw a good pulse, the value of lastGoodAzimuth is set to the currentAzimuth.

If the Tgt_Reached() function returns true, the rotator is stopped and the isRotating flag is set to false and the new currentAzimuth is sent to the LCD, and the targetAzimuth is set equal to the currentAzimuth.

The Tgt_Reached() Function

The Tgt_Reached() function first compares the currentAzimuth to the targetAzimuth and returns true if they are equal.

Because of the goofy azimuth math in Version 3.0, sometimes the currentAzimuth was exceeding the minimum and maximum limits, so the function checks to see if that is the case, and if so, sets the currentAzimuth to either minAzimuth or maxAzimuth appropriately.

However, if the rotator isCalibrating, we don’t do the limit test, as when it is being calibrated, the software forces it to rotate beyond the limits.

The Check_Reversal() Function

The Check_Reversal() function handles the issue of the operator changing the targetAzimuth to a value that would require the rotator to move in the opposite direction from the direction in which it is currently moving. This can be done either via a command from the serial input or via physical movement of the rotary encoder.

- Page 40 -

The logic is simple; if the rotator isn’t moving, we do nothing. If it is rotating, we look to see if the current direction of rotation needs to be reversed based on a comparison of the targetAzimuth and currentAzimuth. If the direction of rotation does need to change, we simply stop the rotator and set the isRotating flag to false. Because the targetAzimuth and currentAzimuth are still not the same, the next call to Start_Rotator() will start it moving again in the proper direction.

Note that this approach increases the probability that the rotator will come to a complete stop before starting it in the opposite direction, thus reducing the mechanical stress on the rotator itself.

The Read_Encoder() Function

The Read_Encoder() function is never called directly from any of the other functions, but rather is invoked by the Arduino’s hardware interrupt capability.

The first thing the Read_Encoder() function does is to look at the state of the isCalibrating flag. If the rotator is being calibrated, we don’t want the operator to be able to change the targetAzimuth while that is happening. Since the Calibrate() function takes control away from the main loop, the operator won’t be able to change the targetAzimuth from the N1MM+ program or the serial monitor either.

The encoder library function process() takes care of determining which direction the operator is turning the knob. Depending on which way the knob is turning, we either increment or decrement the targetAzimuth.

In Version 4.0, the amount that the targetAzimuth is changed depends upon the setting of the front panel toggle switch (if installed).

Note that we also never let the targetAzimuth exceed the minimum or maximum limits.

One thing to note; after we read the encoder there is a test to see which direction the knob is being turned. There is a case statement for DIR_NONE, followed by a return statement. I didn’t think it would actually possible for the interrupt function to be executed if the encoder wasn’t being turned, but, for some reason that I have yet to figure out, as soon as the attachInterrupt() function was called to set up the interrupts for both encoder pins in setup(), the interrupt function was being executed. Testing for no movement and simply exiting the function took care of the issue.

- Page 41 -

Another thing to note is that on some of the encoders available on the internet, the ‘A’ & ‘B’ pins are reversed, which makes the Rotary.process() function think that the encoder is moving in the opposite direction from what it is really doing. The problem is most easily fixed by simply reversing the pin assignments (in the My_Rotator.h file) in the software. The encoders I happened to have on hand have this issue, and thus you will note the pin designations are reversed in my software.

The Say_Hello() Function

The Say_Hello() function is responsible for displaying the message announcing that the controller is running and looking for work to do. It is called on every pass through the loop() function to see if the welcome message needs to be re-displayed.

Anytime anything other than the hello message is displayed (e.g. the targetAzimuth reading or an error message), we set a timer. When that timer expires, we re-display the hello message.

The first thing the function does is check to see if the hello message is already on the display, and if so, it just returns.

Next, we check to see if the helloTimeout since the time some other type of message was displayed has expired. If not, then we return.

After that, it uses the LCD_Display() function to put the hello message on the display and sets a flag indicating that the hello message is, in fact, being displayed.

The Display_Rotation() Function

The Display_Rotation() function lets the operator know the rotator is turning by updating the currentAzimuth on the second line of the display. Note that it does not re-write the entire second line, but rather, just changes the digits.

Note that in Version 3.0, because the azimuths are not nice multiples of 1° that the number stored internally is rounded off before being converted back to a real azimuth to be displayed.

- Page 42 -

The Display_Target() Function

The Display_Target() function displays the targetAzimuth on the first line of the display whenever the rotator is turning (except during calibration).

Again as in the case of the Display_Rotation() function, the internal azimuth is rounded off before being displayed.

The Check_LCD() Function

The Check_LCD() function is called on each pass through the loop() function. It looks for data in the LCD buffers, and if anything is in either one, it uses LCD_Print() to display them.

This approach might seem a bit strange at first, but it solved a problem caused by attempting to use the display directly from the interrupt invoked Read_Encoder() function. Attempting to use the display directly from within that function caused some kind of confusion in the Arduino’s interrupt handling mechanism, which in turn, caused the whole program to lock up.

The problem was solved by having Read_Encoder() simply put messages into the buffers to be picked up in the main loop after Read_Encoder() had completed its work.

The LCD_Print() Function

The LCD_Print() function handles the task of actually displaying something on the LCD display. Arguments are which line to put it on, and what to put there. Note, we allow the caller to specify lines 1 or 2, and convert those to 0 and 1 in the function (just a human factors consideration).

The function first checks to see if the requested line number actually exists on the display being used, and if not, simply ignores the display request.

We then create a standard char[] type buffer to transfer the information to be displayed into. We must do this, as the print functions in the LCD object do not have the capability of handling an argument of the type String (I may fix this somewhere down the road).

- Page 43 -

Lest we cause a problem by attempting to put too much data in the fixed buffer, we make sure the length of the data String we are being asked to display is no longer than the buffer space allocated (which is just enough for the width of the physical display). If it’s too long, we simply truncate it.

After copying the String into the character buffer, we check to see if it’s shorter that the display width. If that is the case, we pad the end of it with space characters. If we didn’t do this, the remnants of a previous message would remain on the display.

Finally, we use the print function built into the LCD object to put the message on the screen.

The Int_2_Az() Function

The Int_2_Az() Function is used whenever we need to display an azimuth reading on the LCD or respond to the “C” command from the N1MM+ program.

This function builds a String containing the ASCII representation of the real azimuth. The String is always a 3 digit number padded with leading zeros if necessary.

Note that the Azimuth argument is expected to be a real azimuth in the range of 0° to 360°, not the internally maintained azimuth.

The Update_Az() Function

The Update_Az() checks to see if the value of the currentAzimuth needs to be updated in the EEPROM. We do not do this every time the currentAzimuth changes for two reasons. First, it takes a really long time to write to the EEPROM. Secondly, the EEPROM has a limited number of times it can be written to before it fails. That is a huge number, but if we were to write the currentAzimuth every time it changed, we could possibly hit that limit over time.

Thus, we only update it after there has been no rotation for EEPROM_TIMEOUT milliseconds.

- Page 44 -

An important note; after the controller has been in use for a while, before turning it off, the operator should make sure that the currentAzimuth has been saved as indicated by the green LED on the front panel. If the unit is turned off without the azimuth having been saved, it will be considerable out of calibration the next time it is turned on.

If the controller in use has the Version 2.1 software and associated wiring changes, pushing the “Reset” button will force the azimuth to be saved.

The Calibrate() Function

The Calibrate() function can be invoked from the command processing logic, however, the N1MM+ program does not use the command for a Yaesu rotator. The function is called, however from the main loop if the pushbutton switch built into the rotary encoder is operated.

Also note that the rotator is pretty much self-calibrating. Anytime a timeout occurs, it is assumed to be due to the fact that the rotator hit the mechanical end stop. Anytime that happens, the Check_Timeout() function sets the azimuths appropriately.

Note that the function takes over total of control from the normal processing in the main loop, so any commands sent from the N1MM+ program will be ignored until the calibration process has completed.

After setting the isCalibrating flag to true (which causes Read_Encoder() to ignore any interrupts), we see which end stop we think we are closer to and set the targetAzimuth to either minAzimuth minus maxAzimuth or maxAzimuth times 2 so as to minimize the time to perform the calibration and ensure that the rotator actually hit the end stop. Note that the assumed direction of rotation needed may or may not be correct depending on how far out of calibration the rotator is.

In previous versions the value of currentAzimuth was used to make this determination, however if a timeout occurred due to just missing a cam pulse that was not a result of hitting the end stop, the value in currentAzimuth could be way off. To fix this, in Version 4.1, a new variable was introduced (lastGoodAzimuth) which is only set after seeing a good pulse. This new variable is used to determine which way to turn to do the calibration.

- Page 45 -

The function mimics the rotator movement logic of the main loop, except we are looking for and expecting a timeout to occur.

When the timeout occurs, we assume that the rotator hit the mechanical end stop, and the logic in the Check_Timeout() function will set the correct values of currentAzimuth and targetAzimuth and stop the motor.

If the timeout occurred, we clear the isCalibrating flag, inform the operator that the rotator is calibrated, and we’re finished.

The Start_Motor() Function

Start_Motor() is pretty simple. We set the direction of rotation based on the value of the Dir argument then after a 10mS pause to allow the contacts in the direction relay (‘K2’) to settle, we activate the power relay (‘K1’).

Once the motor is running, the function sets the appropriate values for the index pulse handling and timeout parameters.

In Version 5.4 and later, the value of rotatorTimeout is set to INITIAL_TIMEOUT (2 seconds). After the software sees two cam switch pulses, the value of rotatorTimeout reverts back to the value of ROTATOR_TIMEOUT.

The Stop_Motor() Function

Stop_Motor() turns the power relay off and after a 10mS pause to allow ‘K1’ to settle down then turns the direction relay (‘K2’) off.

Once the motor is stopped, the function clears the values for the index pulse handling and timeout parameters.

Note, the function accepts a String type argument which will be displayed in the serial monitor if debugging is enabled.

- Page 46 -

The Backup() Function

The Backup() Function was added in Version 2.2. In testing, I discovered that there are more than 360° between the CW and CCW end stops on the rotator. This function is called from the Check_Timeout() function when the rotator does hit the stop, and using a Time parameter (in milliseconds), backs the rotator off the stop by approximately CAL_ADJUSTMENT degrees. It does this on the QT; that is, it doesn’t mess with the azimuth readings or any of the flags associated with normal rotation.

I was also thinking that maybe this should be used whenever the rotator stops due to a HARD_PULSE being received to back it up by the debounce masking time, but so far, haven’t done so.

The Ck_Reboot() Function

Ck_Reboot() looks to see if the reset button on the back panel is operated, and if so, saves the currentAzimuth in the EEPROM and performs a software initiated reboot.

The Blink_LED() Function

Whenever a timeout occurs, either because the rotator hit the end stop unexpectedly or during calibration or when the operator pushes the reset button, this function flashes the azimuth saved LED for a second.

## Tuning the Timing Parameters

Throughout the description of how the software works, there are many places where I mention the values of the various parameters associated with the timing and rotation of the rotator. I figured it would be useful to the reader to consolidate how I arrived at the various numbers in one place.

In order to achieve the most accuracy possible, it is important to tweak these parameters for a particular rotator; again, this is really only necessary if you’re using it on a very narrow pattern antenna; it’s not really going to matter for something like a tribander.

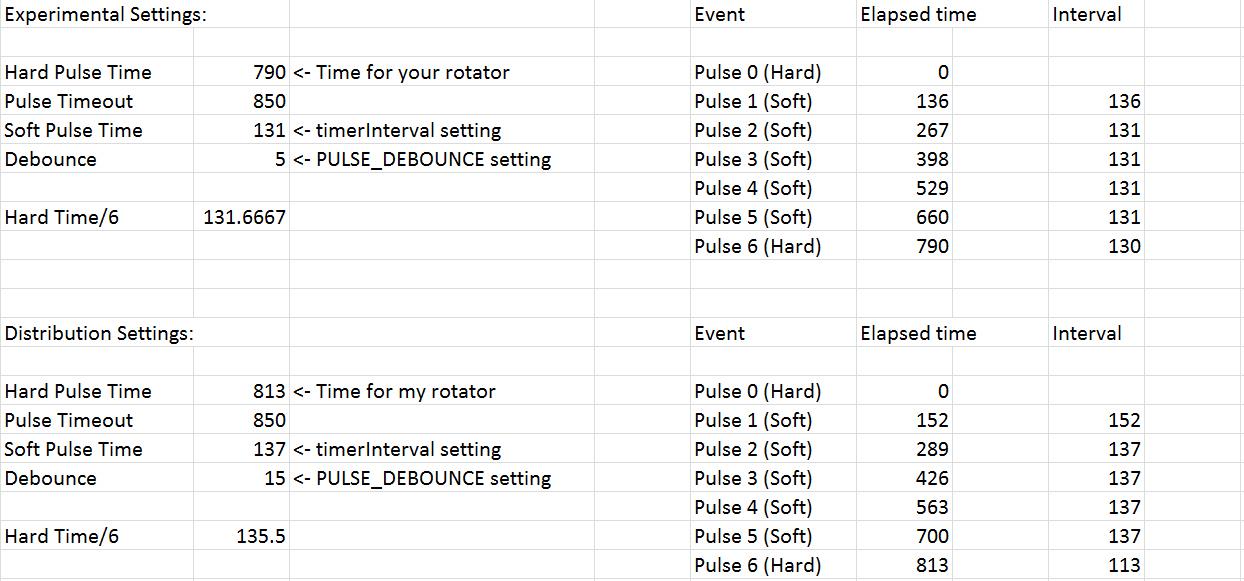
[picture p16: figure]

- Page 47 -

There are three parameters that you can adjust are:

- timerInterval – Time in mS between soft (timer) pulses
- PULSE_DEBOUNCE – delay time after cam (hard) pulse is detected
- ROTATOR_TIMEOUT – Time when we assume we missed a hard pulse

Included in the distribution package is an Excel spreadsheet (Timing.xlsx) which you can use to really fine tune these parameters for your particular rotator.

But before you start, understand a few assumptions:

- Because the amount of rotation between cam pulses is all based on mechanical stuff, we assume that is fairly consistent for all AR-22 rotators.
- The computations in the code are all based on the amount of time between cam switch pulses, which is based on rotational speed. It might be that the rotational speed could vary slightly based on the temperature; I haven’t tested this theory.
Also, different rotators seem to run at slightly different speeds; one of mine turns about 3% faster than the other one.

Here’s what the spreadsheet looks like; all the numbers are milliseconds:

- Page 48 -

The parameter values in the bottom section are the settings in the software as distributed, and they work for both of my rotators.

The data in the top section shows the settings that optimized the performance of the test rotator in my basement. Notice that that one turns a little faster than the one on my roof (790 mS between cam pulses as opposed to 813 mS).

If you look at the rightmost column, you will see that the intervals between pulses with the settings in the distributed software are not all even, whereas those for the test rotator are. Those settings did not work for the slightly slower rotator on the roof.

So to tweak the numbers for your particular rotator, first you need to measure the interval between cam pulses (and note the software triggers off the end of the pulse, not the beginning; there’s a reason for that). The scope trace earlier in the document shows that the hard pulse interval for my test rotator is ~790 mS. Dividing that by 6 gives the number of milliseconds for one degree (actually 0.974°; see next section) of rotation as 131.667 mS, so for that rotator, I set the timerInterval variable to 131000 and it worked great.

The timing between the initial hard pulse and the first soft pulse is PULSE_DEBOUNCE milliseconds longer than the rest as the soft pulse timer is not reset until the pulse is actually processed.

Once you have everything else working, you can experiment with reducing the ROTATOR_TIMEOUT setting although that’s not really critical.

And just for the record, if I didn’t already mention it somewhere else in the document, the reason the Pulse_ISR interrupt is triggered from the trailing edge of the pulse versus the leading edge is the solution to the problem of the rotator hitting the mechanical end stop with the cam switch operated.

Rotational (Cam Switch) Error

Running the rotator using the original clunk-clunk box, I discovered that after commanding the rotator to turn 360°, it was coming up consistently short of turning 360°.

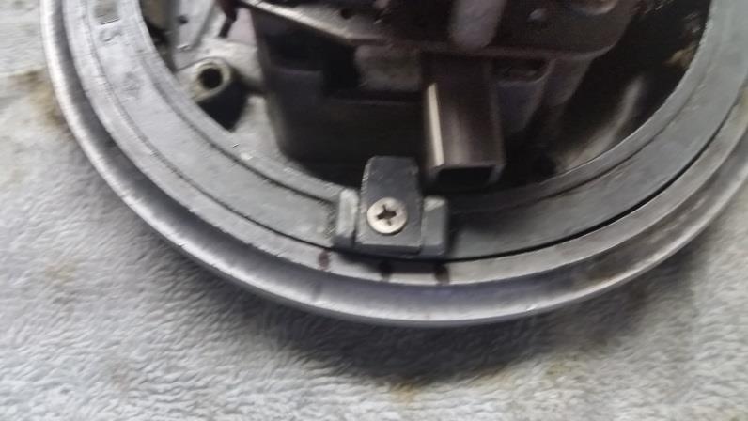
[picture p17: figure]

- Page 49 -

To determine the amount of the error, with the motor assembly removed from the rotator, I marked the rotator as shown in the following picture:

The two outer marks represent the inner sides of the stop arm, and the center mark is halfway in between, which I consider to be the 0°/360° point. Note, the stop pin in my rotator is about twice as wide as the stock one, as mine broke off and I repaired it as shown in the picture. I also had to build a new stop arm, as the original one got mangled. Notice the new one is made of a piece of ½” square steel tubing instead of the ½” x 3/8” U shaped piece that was originally used. I highly recommend this modification whether needed or not. I have 2 AR-22 rotators and the stop arms in both were bent out of shape.

Replacing the ring gear with one made of stainless steel (http://rfjunk.com/Stainless-Ring-Gear-CDE-CDR-HY-GAIN-HYGAIN_p_207.html) is also a good idea. In my #2 rotator, the ring gear was cracked and as shown above, on the #1 rotator, the stop pin broke off.

Using the center mark as a reference, after turning the rotator 360° according to the clunk-clunk box, I measured the distance between where the pin stopped and the center mark. For my rotator, the average error was 0.47”. The diameter of the ring gear is 5.75”, and thus its circumference is 18.06”. In degrees, the amount of error is:

360 x 0.47 / 18.06 = 9.39°

That means that for 60 clicks on the clunk-clunk box, the rotator is only turning 350.61°. The number of cam switch pulses for a full 360° rotation is then:

- Page 50 -

60 x 360 / 350.61 = 61.61 Pulses

Multiplying that by 6 gives the total number of pulses (cam plus timer) need for 360° of rotation as 369.64.

Dividing that by 60 gives us 5.844° for each cam pulse, and dividing that by 6 gives 0.974° for timer pulses.

In the My_Rotator.h file for my rotator, I set the PULSE_DEGREES definition to 5.85 degrees. The timerDegrees value is computed based on that in the setup() function.

Timeout Backup Adjustment

The final variable that will need to be tweaked is the value of the CAL_ADJUSTMENT definition in the My_Rotator.h header file. This value defines the approximate number of degrees to back up the rotator whenever it hits the end stop (either in normal operation or during calibration).

In my version of the code, it is set to 5°. But, as shown in the picture above, my stop pin is about twice as wide as the original, which means that in most cases, the value might have to be increased, although I didn’t bother doing that for the rotator with the standard stop pin and it didn’t really seem to matter.

## Operation

Calibration

Before using the controller, if your rotator is not yet mounted somewhere, you should set it up in the workshop and do the tests described above in the “Tuning the Timing Parameters” section. I’ve built 2 of these controllers, and I’ve tested them with two rotators, one of which, as mentioned has a wider stop tab than the stock rotator. I can’t guarantee that the values I have set for all the timing parameters will work correctly for all rotators.

If you can’t set it up in the workshop and there seems to be issues with the timing parameters, you can still play with them in the software to see if it makes any improvement.

- Page 51 -

Using It

The operation should be pretty much self-explanatory, but I’ll give you a few of the highlights here.

The first time you turn it on, it may read some random number from the EEPROM address where the current azimuth is saved, and thus the first thing to do is to calibrate the controller with the rotator by pressing the encoder switch. The unit will announce that it is “Calibrating” and when finished, it will announce that it is “Calibrated”. Now you’re ready to go.

You can use the (Version 4.0) azimuth increment toggle switch to set the number of degrees that the target azimuth should be incremented or decremented for each click of the encoder. I keep mine set on 5° as I’m using it with a 3 element 6 meter beam, so the azimuth need not be that accurate. If you’re turning a highly directional UHF array, then maybe you would want to use the 1° setting. Note that in the 1° mode, it takes a lot of turns of the encoder to move the antenna any significant amount.

When you move the encoder, the new target azimuth will be shown on the top line of the display, and you will see the current azimuth changing on the 2nd line. When they are equal, the rotation will stop.

10 seconds after the rotation stops (you can change this in the header file) the display will show “Azimuth Saved” on the top line for 3 seconds and the green “Azimuth Saved” LED will light (if you installed it).

Should the rotator prematurely hit the end stop, the controller will stop seeing pulses from the cam switch and will show “Timeout” on the top line of the display. If the “Azimuth Saved” LED is installed it will also flash for about 1 second. When a timeout occurs, the current azimuth will be set to either 0° or 360° based on which way the rotator was turning when the timeout occurred.

## Known Bugs and Glitches

The USB connection was to the PC was dropping. I’d seen it happen when trying to control it via the Arduino IDE’s serial monitor, the N1MM Rotor program and SatPC32. It seems to happen randomly; sometimes when the rotator stops, sometimes in the middle of a rotation and sometimes when not doing anything.

- Page 52 -

Online research indicates that other folks have seen the same problem in other applications. As it doesn’t happen consistently, I’m 99.99% sure it’s not a software problem. The only thing I can think of is that perhaps starting and stopping the motor is causing power fluctuations on the processor.

The hardware changes noted above in Version 5.4 seem to have fixed this problem.

Note, if the controller is wired according to the Version 1.0 or 2.0 schematics, the Reset button does NOT save the azimuth, so make sure it has been saved before performing the reset.

It’s not a bug, it’s a feature! But the operator might think it’s a glitch; when the rotator is being calibrated, it is possible for the display to show a current azimuth of more than 360°. It could also show an azimuth of less than zero, however, the software will convert negative readings to positive azimuths of slightly less than 360°. For example, if the internally maintained currentAzimuth is -006°. It would be displayed as 354°. This is the only case where the azimuth displayed can be outside the 0° to 360° range. It is possible when calibrating, because the rotator itself is not in agreement with the azimuth in the software.

## Coming Attractions

Hardware Enhancements

One hardware enhancement I’m thinking about, although it looks like a lot of work and at least two more wires in the cable, is to replace the mechanical end stop in the rotator with limit switches (like the heavier duty rotators have). The stop mechanism in my test rotator actually broke although I don’t think it was due to the behavior of the smart controller, but rather simply old age. The modification would require some slight software changes.

- Page 53 -

Elevation control

On the Version 5.4 controller PCB, I added a header connected to the Serial2 TX/RX pins on the Arduino Mega. These aren’t used yet, but I have a stepper motor controller built on an Arduino Uno that I’m thinking of adapting as an elevation control for my satellite antenna. My thought is to have the command processing logic send elevation control messages to the 2nd processor.

The hooks for this are already in the Version 5.4 software and can be turned on by setting the symbol ELEVATION in the header file to true. The only effect this has is to enable the Serial2 UART and forward the ‘W’ command to whatever might be connected to that output.

This might change in future versions once I begin designing and building the elevation control unit.

Support for Other Rotators

As previously mentioned, this controller hardware and software would probably work with some slight modifications for the Alliance rotators or any others that use a clunk-clunk type controller.

I looked at the CDE Ham-M rotator manual (http://www.radiomanual.info/schemi/ACC_rotator/CDE_HAM-M_user.pdf) to see if this controller could be adopted to run that rotator. The simple answer is “No”! It would require totally different hardware and a lot of changes to the code.

Having said that, it would be possible to build a similar unit for the Ham-M, and that design would probably also work with the Hy-Gain Ham-IV rotator, (http://www.hayseed.net/~jpk5lad/download/CDE%20Ham%20IV%20rotator.pdf) which has almost identical circuitry to the Ham-M.

- Page 54 -

## Bill of Materials

Main Controller PCB

Parts needed for the main controller circuit board (optional IC sockets are not included):

Processor | Arduino Mega 2560
C1, C3 | 10uF – 50V electrolytic capacitor
C2, C4 | 0.22uF – 50V capacitor
D1 | 1N4002
D2, D3 | 1N4148
R1 | 10Ω – 1/4W
R2 | 470Ω – 1/4W
R3 | 220Ω – 1/4W
J1 | 4 pin female vertical header
J2 | 3 connection screw terminal – 0.2” pin spacing
J3, J11 | 2 pin right angle male headers the PCB is designed so that a single 4 pin header can be used for both.
J4 – J7, J9 | Various pin count right angle male headers; the PCB is designed so that a single 16 pin header can be used for all.
J8 | 4 connection screw terminal – 0.2” pin spacing
J10 | 4 pin vertical male header
3 ea. | 8 pin female vertical header with long pins; connections between the controller board and the Arduino.
1 ea. | 10 pin female vertical header with long pins; connections between the controller board and the Arduino.

- Page 55 -
K1, K2 | Fujitsu NA-5W-K 5V DPDT relay. (https://www.jameco.com/webapp/wcs/stores/servlet/ProductDisplay?catalogId=10001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)
U1 | LCA-110 solid state relay (http://www.ixysic.com/home/pdfs.nsf/www/LCA110.pdf/$file/LCA110.pdf)

Power Supply PCB

These parts are needed for the power supply circuit board:

C1, C4 | 1000uF – 50V electrolytic capacitor
C2, C3 | 100nF ceramic disk capacitor
D1, D2 | 1N4002
R1 | 1.8KΩ ¼ watt resistor
J1 | 2 pin male vertical header
J2 | 4 pin male vertical header
J3, J4 | 8 pin female vertical (stacking type) header with long pins.
U1 | LM7812 voltage regulator (TO-220 package) with additional heat sink

Other Components (Mounted in the Enclosure)

The following parts are not shown on the above schematics, but rather mount on the enclosure used. Many of them connect to the various headers on the controller board or power supply board. The pictures should help you figure it out:

F1 | 2 amp fuse and appropriate holder
S1 | Power switch
S2 | Azimuth switch; SPDT – center off toggle switch

- Page 56 -
S2 | Run/Update switch; SPST toggle switch
S3 | Reset button; SP pushbutton
T1 | 28V – 2A – CT; Hammond model 187E28 (https://www.mouser.com/ProductDetail/Hammond-Manufacturing/187E28?qs=PRAnc%252blXlHhlx%2FRo63C%252bsw%3D%3D) or equivalent. You can also use a Hammond model 187E36 (https://www.mouser.com/ProductDetail/Hammond-Manufacturing/187E36/) (36V – CT) transformer. Both are physically identical.
C1 | Motor starting capacitor (https://www.amazon.com/gp/product/B00EQI3HZ2/ref=od_aui_detailpages00?ie=UTF8&psc=1) - ~145uF – 165VAC
Encoder | Keyes KY-040 Rotary Encoder (http://henrysbench.capnfatz.com/henrys-bench/arduino-sensors-and-input/keyes-ky-040-arduino-rotary-encoder-user-manual/)
Display | I2C 1602 2 line by 16 character LCD display
D1 | General purpose 20mA red LED (power)
D2 | General purpose 20mA green LED (azimuth saved)
Rotator Connection | My controller has both a 4 conductor Cinch-Jones type connector and a barrier terminal strip installed for the connection to the rotator cable. Do whatever suits your personal needs.
Power Connector | I used the type used for PCs as I have a ton of PC power cables on hand!
USB Connector | This is a panel mount female type “B” to male type “B” USB cable. If you want to be able to load software without opening the enclosure or use the controller with PC based software (such as N1MM+), you’ll need this.

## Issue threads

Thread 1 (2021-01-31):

PC Control Problem

WA2FZW, 2021-01-31:
I've discovered a problem in using the controller under PC control. The USB connection keeps dropping. This happens when trying to use the controller with the N1MM Rotor program, SatPC32 and even when just trying to talk to it via the Arduino IDE. Manual mode works fine except operating the controller via the encoder also causes the USB connection to drop. I'm not sure if it's a hardware issue on the latest version of the PCB or a software problem, but I'm working on it!

WA2FZW, 2021-02-14:
So after 2 weeks of futzing around with the software and upgrading the power supply to add a lot more filtering neither of which fixed the problem tonight just for kicks I moved the USB connection from a port on the PC to a spare port on an external USB hub that was also connecting a couple of other things to the PC. Bingo! It ran for an hour and a half with no hiccups!

So the problem has something to do with the PC ports, not the controller.

As soon as I get the documentation updated to describe the hardware and software changes I will publish the new versions of both the hardware and software.  There are no changes in the software that require upgrading the hardware. The hardware changes include adding more filtering to the power supply board and adding a capacitor to the controller board to reduce the noise on the pulse lead from the rotator.

Closed 2021-02-14.

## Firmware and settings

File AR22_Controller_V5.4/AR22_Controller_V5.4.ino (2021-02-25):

/*
 * 	AR22_Controller - Version 5.4
 *
 *	This source file is under General Public License version 3. Please feel free to
 *	distribute it, hack it, or do anything else you like to it. I would ask, however
 *	that is you make any cool improvements, you let me know via any of the websites
 *	on which I have published this.
 *
 *	This program is designed to run on an Arduino Mega 2560. It emulates the interface
 *	between the N1MM Rotor control program and a Yaesu rotator using the GS-232
 *	protocol). Since the N1MM Rotor program does not recognize the AR-22 rotator,
 *	we have to make it think it is talking to something that it does support. A 2nd
 *	choice would have been to emulate the HyGain DCU-1 protocol, however, it does
 *	not have as complete a command set as the Yaesu protocol, and is harder to decipher.
 *	
 *	In Version 1.0, the rotator operated in the same manner as it did with the original
 *	clunk-clunk box; in other words, the azimuth resolution was based solely on the ~6
 *	degree cam operated switch in the rotator.
 *	
 *	In Version 2.0, we added a timer interrupt set to trigger approximately every 140mS,
 *	which is just slightly longer than the rotator takes to turn 1 degree. We treat
 *	the timer interrupt as if it were a regular index pulse (except for reseting the
 *	timeout). When a hard pulse is received, we will reset the timer and timeouts.
 *	
 *	For Version 2.1, we made a hardware change. Rather than the back panel reset button
 *	being connected to the Arduino's reset pin, we moved it to a digital pin (D18) and
 *	use a software reset along with a forced save of the "currentAzimuth" before restarting.
 *	Note that controllers wired for the hard reset can still use this software.
 *	
 *	In Version 3.0, I moved the definitions of variables that might need to be tweaked
 *	based on characteristics of a particular rotator to the "My_Rotator.h" header file.
 *	
 *	More significantly, in trying to determine why the rotator was not turning a full 360
 *	degrees with the clunk-clunk controller, it was discovered that the cam switch was
 *	actually sending pulses about every 5.85 degrees as opposed to the advertised 6 degrees.
 *	In Version 3.0, the azimuth math has been totally overhauled to deal with this issue.
 *	
 *	Part of the overhaul of the azimuth math involves maintaining all azimuth related values
 *	in the program multiplied by 1000 (defined in "My_Rotator.h" as "timerDegrees").
 *
 *	In Version 4.0, a number of hardware and software changes are made. In the hardware, we
 *	added a 3 position toggle switch which is used to select the size of the azimuth increment
 *	(or decrement) for each click of the encoder. After finally getting to use the controller
 *	during a contest where many azimuth changes were made only being to change the azimuth one
 *	degree at a time was a pain! The switch allows you to select 1, 5 or 10 degree increments.
 *
 *	Another hardware change is to add a LED that indicates the current azimuth has been saved
 *	in the EEPROM. This LED will also flash for about a second whenever a timeout occurrs.
 *
 *	Software changes in Version 4.0 include support for the above hardware changes and a
 *	minor change in the azimuth save logic. I discovered that when making large azimuth
 *	changes, sometimes you stop turning the knob briefly and the azimuth gets saved before the
 *	entire change has completed. We will now wait a few seconds after the rotator has stopped
 *	turning before saving the azimuth. The delay is currently set to 10 seconds in the
 *	"My_Rotator.h" file. It can be changed to whatever you like. We also eliminated the 1
 *	minute minimum between EEPROM saves.
 *
 *	I also changed the naming conventions of all defined things and variables to match the
 *	standard coding conventions.
 *
 *	In Version 4.1, I made a change in the calibration procedure. Previously, the "calibrate()"
 *	function used a comaparison between the current aximuth the maximum and minimum azimuths to
 *	take a guess as to which way to turn to accomplish the procedure. If the rotator got out of
 *	calibration due to a missed hard pulse, the current azimuth would be at either the maximum
 *	or minimum and would sometimes turn 3/4 or more of the way around to calibrate.
 *
 *	The fix is to add a new variable: "lastGoodAzimuth" which will be updated everytime a pulse
 *	is seen during normal rotation. This variable will also be set at the end of a calibration
 *	cycle, but not during calibration.
 *
 *	Version 5.0 made some changes in pin assignments for compatibility with the PCB that
 *	replaced the hand-wired controller board.
 *
 *	Version 5.1 just fixes a couple of bugs.
 *
 *	In Version 5.4, I changed a number of things (including the hardware) in an attempt
 *	to fix the problem of the USB connection between the controller dropping and a few
 *	other things:
 *	
 *		First, I changed the timeout logic which fixed a couple of problems when the
 *		motor is first started:
 *
 *			1.	With a large antenna, there is some startup inertia which needed to be
 *				compensated for.
 *			2.	If the rotator happened to have stopped with the cam switch in the
 *				closed position we were seeing an immediate pulse and an immediate
 *				timeout occurred.
 *
 *		Secondly, I added code to turn off the timer interrupts when a timeout occurs
 *		or when the motor is stopped.
 *
 *		The other major change was to eliminate the command translation table and to
 *		combine the original "Get_Command" and "Process_Command" functions into a
 *		single function.
 *
 *		Finally, I added all the hooks for the interface to an elevation controller
 *		for my satellite antenna.
 */

/*
 *	Setting "DEBUG" to "true" will turn on a lot of print statements that show you
 *	what the program is thinking. It should only be enabled if you are using the
 *	Arduino IDE's serial monitor (or some other terminal emulator) to talk to it as
 *	the debug outputs are likely to confuse other programs such as N1MM Rotor or
 *	SatPC32.
 */

#define	DEBUG	false				// Enables verbose output when set to "true"

#include "My_Rotator.h"				// Things that might have to be tweaked.


/*
 *	Summary of Arduino input/output pin usage:
 *
 *		D0		USB Interface Receive
 *		D1		USB Interface Transmit
 *		D2		ENCODER_PIN_B
 *		D3		ENCODER_PIN_A 
 *		D4		CAL_SWITCH (encoder pushbutton)
 *		D5	 	1 degree switch
 *		D6		10 degree switch
 *		D8		Azimuth saved LED (on when the "currentAzimuth" is saved in the EEPROM)
 *		D9		MOTOR_DIRECTION
 *		D10		MOTOR_RUN
 *		D11		-|
 *		D12		 |- Reserved for Timer1 PWM output signals
 *		D13		-|
 *		D16		Serial2 Transmit line (reserved for future use)
 *		D17		Serial2 Receive line (reserved for future use)
 *		D18		MOTOR_INDEX (Interrupt enabled pin )
 *		D19		Software Reset
 *		D20		LCD_SDA (Data)				
 *		D21		LCD_SCL (Clock)
 */


/*
 *	Define the pin assignments and other stuff for the rotator
 */

#define	MOTOR_DIRECTION	 9				// Relay (K2) to select direction of rotation
#define	MOTOR_RUN	 	10				// Relay (K1) to power the rotator
#define MOTOR_INDEX	    18				// 6 degree indicator (interrupt enabled)

#define	ONE_DEGREE	     5				// When LOW, each encoder click is 1 degree
#define TEN_DEGREE       6				// When LOW. each encoder click is 10 degrees
										// If neither is LOW, each click is "DEFAULT_INCR" degrees

#define	SAVED_LED		 8				// Operates LED to show azimuth is saved
#define	LED_ON	HIGH					// By defining the on and off conditions this
#define	LED_OFF	LOW						// way I don't have to remember what they are!

#define	STOP	LOW						// Stop the motor
#define	RUN		HIGH					// Run the motor

#define	CW		LOW						// Rotate clockwise
#define	CCW		HIGH					// Rotate counter-clockwise
#define	OFF		LOW						// Alternate definition to turn relays off

bool			directionRelay  = OFF;		// Direction relay is off
volatile bool	isRotating 		= false;	// True when rotation in progress


/*
 *	Define the pulse types. See "My_Rotator.h" for the definition of the timer pulse
 *	interval and degrees of rotation parameters.
 */
 
volatile uint8_t	pulseType;				// Real, fake or none

#define				NO_PULSE	0			// No pulse seen
#define				HARD_PULSE	1			// Pulse from cam switch
#define				SOFT_PULSE	2			// Timer generated pulse


/*
 *	There are a number of timeout conditions we need to deal with.
 *
 *	1).	When the rotator is turning, we expect to see periodic index pulses from the cam
 *		operated switch. The actual time for the rotator used for testing is about every
 *		784 mS). If that doesn't happen within the alloted time ("ROTATOR_TIMEOUT"), we
 *		assume that it was out of calibration, and it hit the mechanical end stop.
 *
 *	2).	Hello message delay time. When we have nothing of importance to tell the operator about,
 *		we put the default message on the top line of the display. However, if there is something
 *		of importance there, or while the rotator is turning, we don't want to overwrite it until
 *		the operator has had a few seconds to read it.
 *
 *	3).	In version 4.0, we dropped the 1 minute minimum time between EEPROM updates and instead
 *		wait 10 seconds after "rotatorStopTime" before doing the write. This keeps the EEPROM
 *		from being updated until we're pretty sure the operator has finished tweaking the
 *		azimuth.
 *
 *	4). As noted above, in Version 5.4 I added a longer timeout (2 seconds) when the motor first
 *		starts.
 *
 *	The following definitions set the parameters for all the timeouts:
 */

volatile uint32_t	systemTime;					// Since millis() doesn't work in ISRs

volatile uint32_t	pulseTime    = 0;			// Time of last index pulse for timeout function
volatile uint32_t	debounceTime = 0;			// Time of last index pulse for pulse processing logic
volatile uint32_t	rotatorTimeout;				// Cam pulse timeout is variable now
volatile uint16_t	hardPulseCount = 0;			// Counts cam switch pulses

uint32_t			notHelloTime    = 0;		// Last time something other than hello displayed
uint32_t			helloTime       = 0;		// Current time
uint32_t			helloTimeout    = 3000;		// 3 second refresh delay
bool				helloMsg        = false;	// True when the default message is on line 1 of the LCD

uint32_t			rotatorStopTime = 0;		// Last time rotator stopped turning
bool				azChanged       = false;	// True when currentAzimuth has changed
volatile bool		tgtChanged      = false;	// True when targetAzimuth has changed


/*
 *	These are computed based on the value assigned to the symbol "PULSE_DEGREES"
 *	in the header file:
 */

int32_t	timerDegrees;			// Degrees of rotation for each pulse
int32_t	maxAzimuth;				// Maximum allowed azimuth
int32_t	minAzimuth;				// Minimum allowed azimuth


/*
 *	The target and current azimuths keep track of where the rotator is and where we 
 *	want it to be. Anytime they are not the same, the rotator will start turning. Note
 *	the numbers are all stored internally as "long" integers as the numbers will be
 *	much larger than 32K. The math is all done as integer math; Arduinos suck at doing
 *	floating point accurately!
 */

volatile int32_t	targetAzimuth;				// Target azimuth
int32_t				currentAzimuth;				// Current azimuth
int32_t				lastGoodAzimuth;			// Last known good azimuth
int32_t				deltaAzimuth;				// Used in rotating logic
int32_t				azMultiplier;				// Value set by toggle switch
	
#define				AZIMUTH_ADDRESS	0			// EPROM Address for stored "currentAzimuth"

volatile bool		isCalibrating = false;		// True when calibration is in progress


/*
 *	These buffers are used to queue stuff to be displayed on the LCD. Attempting to
 *	update the display from within the "Read_Encoder()" interrupt handling function caused
 *	the whole system to lockup because of how the Arduino handles interrupts. Use of the
 *	"String" class makes handling the strings easier than if we had used "char" arrays.
 */

String	lcdBuffer_1;						// Line 1 buffer
String	lcdBuffer_2;						// Line 2 buffer


/*
 *	Define most of the various strings to be displayed on the LCD (some are built
 *	piecemeal in the code), but these are the fixed ones
 */

#define	helloString			"AR-22 Controller"			// Normal first line of display
#define versionString		"  Version 5.4   "			// Curent software version
#define	currentAzString		"Current Az:  "				// Normal 2nd line
#define	targetAzString		"Target  Az:  "				// Line 1 when rotator is moving
#define timeoutString		"*** Timeout  ***"			// Line 1 when rotator timed out
#define	azSaveString		"* Azimuth Save *"			// Line 1 when saving currentAzimuth
#define	calibrateString		"* Calibrating * "			// Line 1 when calibration in progress
#define	calibratedString	"*  Calibrated  *"			// Line 1 when calibration is finished


/*
 *	Define a few other miscellaneous variables
 */

String	commandBuffer;						// For reading commands from USB port
String	workBuffer;							// General use buffer


/*
 *	If the elevation processor is attached, we need a buffer for messages coming from
 *	it:
 */

#if ( ELEVATION )

String	elevRxBuffer;						// For responses from the elevation processor

#endif

#define SOFT_RESET_PIN 19					// LOW is for software reset (interrupt enabled pin)
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
void loop ()
{
	systemTime = millis ();						// millis() isn't reliable in ISR functions
	
	Say_Hello ();								// See if we need to redisplay the normal line 1

	Get_Command ();								// Get a command and process it (if any there)


/*
 *	Eventually, the next few statements should be moved into a separate function, but
 *	as this is all still in the experimental stage, we'll leave it inline for now.
 *
 *	What we're doing (if the elevation processor is attached) is to see if it has anything
 *	to say that needs to be sent back to the controlling program on the PC.
 */

	if ( ELEVATION )
	{
		if ( Serial2.available () )				// Anything to read?
		{
			elevRxBuffer = Serial2.readStringUntil ( '\r' );	// Read the entire response
			Serial.print ( elevRxBuffer );						// Send it to the PC
			Serial.print ( '\r' );								// Along with a carriage return
		}
	}


/*
 *	As we don't allow the operator to change the position of the target azimuth increment
 *	selector switch while the encoder is being operated or while the rotator is turning, we
 *	will set the "azMultiplier" here. If the switch is not installed or is in the center-
 *	off position, the increment is determined by the value of "DEFAULT_INCR" (defined in
 *	the "My_Rotator.h" file).
 *
 *	Disabling the interrupts fixed an issue where an encoder interrupt occurred in the
 *	middle of reading the switch which sometimes caused a click of the encoder to change
 *	the target asimuth by the wrong amount.
 *
 *	This code only compiles if the switch is installed.
 */

#if AZ_SW_INSTALLED										// If the switch is installed

	if ( !isRotating )									// Only if not turning
	{
		noInterrupts ();								// Disable interrupts

		azMultiplier = DEFAULT_INCR;					// Assume default azimuth increment

		if ( digitalRead ( ONE_DEGREE ) == LOW )		// One degree per click selected?
			azMultiplier = 1;							// Yep!

		else if ( digitalRead ( TEN_DEGREE ) == LOW )	// Ten degrees per click selected?
			azMultiplier = 10;							// Yes it is!

		interrupts ();							// Interrupts ok again
	}

#endif											// #if AZ_SW_INSTALLED

	Display_Target ();							// Only if changed
	Start_Rotator ();							// If necessary, turn the rotator

	if ( isRotating )							// These only need checked if turning
	{
		rotatorStopTime = systemTime;			// Rotator is still turning
		Check_Timeout ();						// Check for rotator timeout
		Read_Pulse ();							// Check for an index pulse
		Check_Reversal ();						// See if we need to reverse direction
	}

	else										// If not rotating
	{
		Update_Az ();							// Update display and maybe the EEPROM
		Check_LCD ();							// Anything to display?
	}

	if ( digitalRead ( CAL_SWITCH ) == LOW )	// Operator want to do calibration?
		Calibrate ();							// Yes, then do it

	Ck_Reboot ();								// Operator want to reboot?
}


/*
 *	"Get_Command" was totally overhauled in Version 5.4. In earlier versions of the 
 *	software it simply read a command from the serial port and translated the character
 *	to a number from the "commandTable".
 *
 *	In Version 5.4, the translation process and the "Process_Command" function were
 *	eliminated. "Get_Command" now also processes the command.
 *
 *	Also in version 5.4, I added handling for the 'W' command. This command requests
 *	both an azimuth and elevation change. The format is "waaa ee". We process it
 *	just like the 'M' command, but then forward it to the elevation controller if that
 *	option is enabled. As near as I can tell this is the only command used by the
 *	SatPC32 program that the elevation controller is interested in.
 *	
 *	Note that the N1MM Rotor program uses a return ('\r') character as a command line
 *	terminator as opposed to the newline character ('\n') generally used by "C" language
 *	programs, thus we use the "Serial.readStringUntil()" function to read the command line.
 *
 *	Also note that if using the Arduino IDE serial monitor (or other terminal emulator)
 *	to send commands, the terminator (button at the bottom of the screen) needs to be set
 *	for "Carriage Return".
 *	
 *	When using the serial monitor, the command letters may be entered in either upper
 *	or lower case.
 */

bool Get_Command ()
{
char command;									// The command character

	if ( !Serial.available () )					// Anything to read?
		return false;							// Nope!

	command = toupper ( Serial.peek () );		// Get the command letter & translate to upper case

	commandBuffer = Serial.readStringUntil ( '\r' );	// Read the entire command for later use

	if ( DEBUG )
	{
		Serial.print ( "Command = " );		Serial.print ( command );
		Serial.print ( ",  Buffer = " );	Serial.println ( commandBuffer );
	}


/*
 *	The "command" variable now contains the single character command letter and the
 *	"commandBuffer" contains the entire command line.
 */

	switch ( command )
	{
		case	'C':							// Respond to request for current azimuth
		{
			workBuffer = "AZ=";
			workBuffer += Int_2_Az (( currentAzimuth + AZ_ROUNDING ) / timerDegrees );
			workBuffer += '\r';					// Add a carriage return

			Serial.print ( workBuffer );		// Send the answer


/*
 *	If in debugging mode, we also output a newline which makes the output easier
 *	to read on the screen:
 */

			if ( DEBUG )
				Serial.print ( '\n' );

			Serial.flush ();						// Make sure everything gets sent
			break;
		}

		case	'M':								// Turn to specified azimuth
		case	'W':								// Azimuth + elevation
		{
			workBuffer = commandBuffer.substring ( 1, 4 );		// Should be 3 digit azimuth
			targetAzimuth = workBuffer.toInt ();				// Make it a number

			targetAzimuth *= timerDegrees;			// Internal representation

			if ( targetAzimuth < minAzimuth )		// Shouldn't happen
				targetAzimuth = minAzimuth;

			if ( targetAzimuth > maxAzimuth )		// Also shouldn't happen
				targetAzimuth = maxAzimuth;

			tgtChanged = true;						// Signal to update the display

			if ( ELEVATION && ( command == 'W' ))	// Does this need to go to the elevation controller?
			{
				Serial2.print ( commandBuffer );	// Yes forward command to it
				Serial2.print ( '\r' );				// And add a carriage return
			}

			break;									// Done
		}

		case	'S':								// Cancel current command
		case	'A':								// Stop rotation
		{
			targetAzimuth = currentAzimuth;			// whever we are is now the target
			Stop_Motor ( "Cancel" );				// Turn motor off
			break;
		}

		case	'Z':								// Initialize azimuths
		{
			workBuffer = commandBuffer.substring ( 1, 4 );	// Should be 3 digit azimuth
			targetAzimuth = workBuffer.toInt ();			// Make it a number

			targetAzimuth *= timerDegrees;					// Internal representation

			if ( targetAzimuth < minAzimuth )				// Shouldn't happen
				targetAzimuth = minAzimuth;

			if ( targetAzimuth > maxAzimuth )				// Also shouldn't happen
				targetAzimuth = maxAzimuth;

			currentAzimuth = targetAzimuth;					// Make them equal
			
			azChanged = false;								// Unchanged since last save

			EEPROM.put ( AZIMUTH_ADDRESS, currentAzimuth );	// Save current azimuth
			digitalWrite ( SAVED_LED, LED_ON );				// Turn on azimuth saved LED

			lcdBuffer_1 = azSaveString;

			break;								// Done
		}

		case	'L':							// Start counter-clockwise rotation
		{
			targetAzimuth = maxAzimuth;			// Open-ended move toward 360 degrees
			tgtChanged = true;
			break;
		}

		case	'R':							// Start clockwise rotation
		{
			targetAzimuth = minAzimuth;			// Open-ended move toward 0 degrees
			tgtChanged = true;
			break;
		}

		case	'F':							// Perform calibration
		{
			Calibrate ();						// Just do it!
			break;
		}

		default:
			break;
	}											// End of command processing "switch"

	command = "";								// Clear them for the next time
	commandBuffer = "";
}


/*
 *	Start_Rotator checks to see if we need to actually turn the rotator. If the 
 *	"currentAzimuth" and "targetAzimuth" are not equal, then we need to turn it. If
 *	the "targetAzimuth" is less than the "currentAzimuth", we need to turn the rotator
 *	clockwise. If the "targetAzimuth" is greater than the "currentAzimuth", we need to
 *	turn the rotator counter-clockwise.
 *
 *	When we initiate the motion, we also set the time at which the motion started. The
 *	"Check_Timeout" function, which is called from the main loop will check to see if
 *	the "rotatorTimeout" value has been exceeded. If that happens, we assume that
 *	the rotator has hit the mechanical end stop in whichever direction it was turning.
 */
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

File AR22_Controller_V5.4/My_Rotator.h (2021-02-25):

/*
 * 	My_Rotator.h - Version 5.4X
 *
 *	This source file is under General Public License version 3. Please feel free to
 *	distribute it, hack it, or do anything else you like to it. I would ask, however
 *	that is you make any cool improvements, you let me know via any of the websites
 *	on which I have published this.
 *	
 *	This header file is used by the AR22 Controller Version 4.0 software. There are a
 *	few variables that might need to be tweaked based on the characteristics of any
 *	specific rotator and/or hardware used to build the smart controller. Those variables
 *	and explanations of why and how to change them are included here.
 *
 */

#ifndef My_Rotator_h				// Prevent double #include
#define My_Rotator_h

/*
 *	Libraries needed:
 */

#include <Rotary.h>					// From https://github.com/brianlow/Rotary
#include <LiquidCrystal_I2C.h>		// From https://github.com/fdebrabander/Arduino-LiquidCrystal-I2C-library
#include <TimerOne.h>				// From https://github.com/PaulStoffregen/TimerOne
#include <SoftReset.h>				// From https://github.com/WickedDevice/SoftReset
#include <Wire.h> 					// Built-in
#include <String.h>					// Built-in
#include <EEPROM.h>					// Built-in


/*
 *	Baud rate selection added in Version 5.4:
 *
 *		It seems the software has a problem working with the N1MM Rotor program which can
 *		only run at 9600 baud, It seems to work fine with the SatPC32 rotator interface
 *		(ServerSDX) running at 57600 baud.
 */

// 	#define BAUD_RATE	57600				// For SatPC32
 	#define	BAUD_RATE	 9600				// For N1MM Rotor


/*
 *	The "ELEVATION" symbol is added in Version 5.4X. If set to "true" hardware serial 
 *	port #2 is used to communicate with a second processor responsible for providing
 *	elevation control for the antenna.
 *
 *	This is purely experimental at the moment as there are a lot of details to be
 *	worked out once we can determine what commands the SatPC32 program uses to send
 *	elevation commands (there are a number of options)! The baudrate for the second
 *	serial port will be the same as for the primary (USB) port.
 */

	#define	ELEVATION	true


/*
 *	While in the process of doing some detailed analysis of why my rotator wasn't
 *	turning a full 360 degrees using the original clunk-clunk box, it turned out
 *	that the cam switch in my rotator was not putting out pulses every 6 degrees
 *	as advertised, but rather every 5.85 degrees. This causes the rotator to come
 *	up a little over 9 degrees short after 60 clicks of the clunk-clunk box.
 *
 *	This meant completely revising the azimuth calculations in the main AR-22
 *	program. The following definitions control the number of degrees we add to or
 *	subtract from the Current_Azimuth for each pulse (cam or timer) we receive.
 *	The numbers are all multiplied by 1000 to avoid having to convert the math to
 *	floating point. But we do have to use "long" integers for the math because the
 *	numbers will be much larger than 32K.
 *
 *	Whenever we read in a normal azimuth (from N1MM+ or the serial monitor), it will
 *	be multiplied by "timerDegrees". Conversely, whenever we need to display an
 *	azimuth, the internal number will be divided by "timerDegrees".
 *
 *	"timerDegrees" along with "maxAzimuth" and "minAzimuth" are calculated in "setup()"
 *	based on the value of "PULSE_DEGREES".
 */

#define	PULSE_DEGREES	5850L	// 5.85 (x 1000) degrees per cam pulse
#define	AZ_ROUNDING		 500L	// Used in the azimuth display functions


/*
 *	"timerInterval" determines the interval between interrupts from the TimerOne library
 *	in microseconds.
 *	
 *	The rotator I used for testing and development took about 50 seconds to complete
 *	a 360 degree rotation. Pulses from the cam operated switch were seen an average of
 *	every 784Ms. The value of "timerInterval" should be set to about 4 - 5% longer than
 *	1/6 of the interval between cam pulses. This ensures that no more and no less than
 *	5 timer pulses will be seen between cam switch pulses.
 *	
 *	The value that seems to work for both of my rotators was determined to be 140Ms.
 */

	volatile uint32_t	timerInterval = 140000;		// Generate interrupts every 137mS


/*
 *	"CAL_ADJUSTMENT" is the number of degrees to back off the end stop whenever the rotator
 *	hits the end stop. I have it set to 5 degrees for my rotator, but the stop tit on
 *	mine is about twice the width of the stock one. Interestingly enough, the way the
 *	rotator is designed, there are actually more than 360 degrees stop to stop, thus
 *	it's never actually calibrated accurately.
 */

#define	CAL_ADJUSTMENT 5


/*
 *	These 2 variables are related to the cam switch pulses.
 *	
 *	The cam switch has a lot of contact bounce. On the rotator used for development and
 *	testing, the cam switch sent a series of pulses between 5 and 10Ms long over a period
 *	of about 50Ms. The setting of "PULSE_DEBOUNCE" masks all but the first state transition
 *	in the series of pulses, so that the software only sees one pulse for each operation
 *	of the cam switch.
 *
 *	Although the Version 05.2 hardware design almost completely eliminated the need to
 *	debounce the cam pulses, but I left in in the code in case it's really needed. On
 *	one of my rotators, I lowered it to 5mS based on the spreadsheet computations that
 *	are described in the documentation.
 *	
 *	Again, my rotator sent cam switch pulses approximately every 784Ms, so the setting of
 *	the "rotatorTimeout" is 850 milliseconds.
 *
 *	"INITIAL_TIMOUUT" is added in Version 5.4. We use it at the initial motor start up, and
 *	after we have seen 2 hard pulses, switch to the normal timeout. This cures two problems:
 *
 *		1.	With a big antenna, there is some startup inertia that must be compensated for.
 *		2.	If the rotator happened to stop with the cam switch operated, it was immediately
 *			timing out.
 */

	#define	PULSE_DEBOUNCE	  15L				// Debounce limit = 15 mS
	#define	ROTATOR_TIMEOUT	 850L				// Timeout between cam pulses
	#define	INITIAL_TIMEOUT	2000L				// Extra delay on motor startup for inertia


/*
 * 	Define the characteristics for the I2C LCD Display. The pin definitions are standard
 * 	for the Arcuino Mega 2560, and should not need to be changed.
 * 	
 * 	The next two variables define the height and width of the display. If a 4x20 display
 * 	were to be used, those should be changed appropriately.
 * 	
 * 	The final variable is the I2C address of the display. 0x27 is the standard address,
 * 	however some of the ones I purchased on the internet came with an address of 0x3F.
 * 	There is a program available on GitHub (https://gist.github.com/tfeldmann/5411375)
 * 	that will scan for I2C devices and report the addresses of any found, if you're
 * 	not sure of the display's address.
 */

	#define LCD_SDA		  20			// Data line
	#define LCD_SCL 	  21			// Clock line
	#define LCD_HEIGHT 	   2			// 2 Lines high
	#define LCD_WIDTH 	  16			// 16 characters wide
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
